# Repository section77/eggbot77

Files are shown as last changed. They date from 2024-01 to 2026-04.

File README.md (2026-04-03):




# eggbot77

Section77-Variante des EggBots mit ESP32 S2 mini

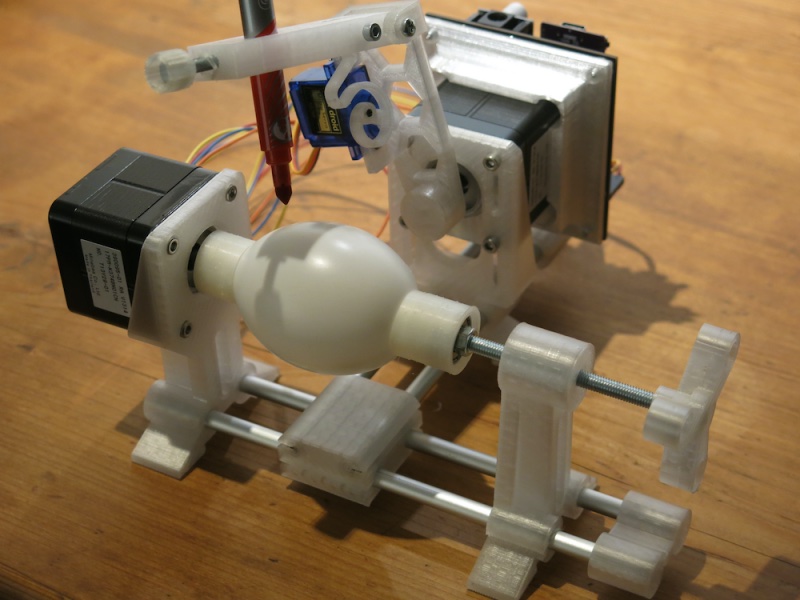
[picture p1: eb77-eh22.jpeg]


Willkommen! :)

Bitte prüfe zuallererst, ob Du alle Komponenten hast, die Du zum Bau Deines EggBot77 brauchst!
* [Materialliste Mechanik](./mechanics/BOM.md)
* [Materialliste Elektronik](./electronics/BOM.md)

Alles da? Super! Dann kann's ja losgehen:
* [Aufbauanleitung Mechanik](./mechanics/assembly/README.md)
* [Aufbauanleitung Elektronik](./electronics/assembly/README.md)
* [Installationsanleitung Firmware](./firmware/README.md)
* [Installationsanleitung Inkscape Plugin](./inkscape_1.x_extension/README.md)

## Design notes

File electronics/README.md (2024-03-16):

Section77 Variante des EggBots mit S2 mini ESP32

Gedanken/Designentscheidungen

## LM2596 Board 1,29€/Stk

für Eingangsspannung -> 5V

Gibt es in zig Varianten, ich habe 20x https://www.amazon.de/Stromversorgung-Spannungsregler-Abwärtswandler-Hocheffizienter-Einstellbares/dp/B07F38DJLS bestellt
Beim Artikel steht Innovateking-EU, ‎Zhovee ‎KKK20 aber keine Aufschrift auf dem Board.

Achtung: Ausgangsspannung am Trimmer einstellen, bevor die anderen Module wie ESP, Schrittmotortreiber, Servo usw. gesteckt werden.
Laut einigen Berichten, muss man mindestens 5 Umdrehungen machen, bevor sich die Ausgangsspannung ändert.

## A4988 carrier board

Ich weiß nicht, was das "original" ist, vermutlich https://www.pololu.com/product/1182
aber es gibt da mittlerweile dutzend Nachbauen, von denen vermutlich viele pinkompatibel sind.
Wir bestellen vermutlich bei https://www.roboter-bausatz.de/p/a4988-schrittmotorentreiber

Microstepping über Lötbrücken einstellbar.

## Netzteile

* https://www.pollin.de/p/polsat-gp1220-a-schaltnetzteil-12-v-2-a-gebraucht-352884 (12V, 2A, Hohlstecker 5,5/2,3 mm, Pluspol innen) - 1,99
* https://www.pollin.de/p/schaltnetzteil-telekom-da-24r12-aaaa-12v-2a-schwarz-352354 (12V, 2A, Hohlstecker 5,5/2,5 mm, Pluspol innen) - 2,50
* https://www.pollin.de/p/stecker-schaltnetzteil-hw-120250eaw-12-v-2-5-a-353145 (12V, 2,5A, Hohlstecker 5,5/2,3 mm, Pluspol innen) - 2,50
* https://www.pollin.de/p/stecker-schaltnetzteil-umec-up0301b-12pe-12v-2-5a-352707 (12V, 2,5A, Hohlstecker 5,5/2,5 mm, Pluspol innen) - 2,95
* https://www.pollin.de/p/stecker-schaltnetzteil-umec-uh0301p-12pe-12v-2-5a-352708 (12V, 2,5A, Hohlstecker 5,5/2,5 mm, Pluspol innen) - 2,95

Hohlbuchsen: Pollin 94-451810 und 94-452316

## S2 mini von Wemos

https://www.wemos.cc/en/latest/s2/s2_mini.html

Für das Board gibt es wohl keine Zeichnung mit Dimensions, siehe auch hier,
wo einer viele Messungen gemacht hat und auch ein Kikad Symbol angefangen hat:
https://gitlab.com/kicad/libraries/kicad-footprints/-/merge_requests/2904

S3 mini hat angeblich gleiches Layout (aber anderes pinning): https://www.wemos.cc/en/latest/_static/files/dim_s3_mini_v1.0.0.pdf

## Stift Servo

um den Stift anzuheben bzw. abzusenken.
Vermutlich https://www.roboter-bausatz.de/p/sg90-9g-micro-servomotor

## Schrittmotoren

Pollin Stepper 94-310690

## Levelshifter

* https://learn.sparkfun.com/tutorials/bi-directional-logic-level-converter-hookup-guide/all
* https://www.digikey.de/de/blog/logic-level-shifting-basics

## Ähnliches Projekt

https://content.instructables.com/FQ1/O4B9/KTWY3YCQ/FQ1O4B9KTWY3YCQ.jpg

Folgende Änderungen:
* SD-Reader entfällt
* Dev-Board durch S2 mini ersetzen
* den 7805 durch step-down ersetzen
* alles sollte THT sein, damit's einfacher zu löten ist

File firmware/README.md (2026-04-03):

## Arduino IDE projects in this directory

* hardware_test: simple programm to check the eggbot77 hardware (both stepper and pen servo) without PC.
  **Attention:** The stepper motors make several fast revolutions. The program should therefore only be executed as long as the servo and stepper motors have not yet been installed.
* EggBott77: firmware which interprets the EBB command set send from the inkscape extension

## Arduino IDE settings common for all projects here

* USB CDC On Boot: "Enabled"
* Controller: LOLIN S2 Mini

## Versions that we have tested successfully with

* Arduino IDE: 2.3.8 (latest as of 2026-03-30)
* esp32: 3.3.7 (latest as of 2026-03-30)

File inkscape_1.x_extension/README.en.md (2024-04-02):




# Inkscape 1.x Extension for EggBot77

## Installation on Linux and OSX
Put the content of the directories `extensions` and `templates` inside the respective folders inside your user extensions folder (the ones listed at `Edit` > `Preferences` under `System: User extensions` and `System: User templates`, by default `~/.config/inkscape/extensions` and `~/.config/inkscape/templates`).

```bash
mkdir -p ~/.config/inkscape/extensions/
mkdir -p ~/.config/inkscape/templates/
cp -r extensions/* ~/.config/inkscape/extensions/
cp -r templates/* ~/.config/inkscape/templates/
```

### Dependencies

- Inkscape >= 1.0 (obviously). We have tested with newer versions up to Inkscape 1.3
- python3
- python3-serial

Note: in case you want to install a newer version of Inkscape, make sure you use the PPA option.

On Debian or Debian-based distributions (Ubuntu, Mint) use apt, for example
```bash
sudo apt install inkscape python3 python3-serial
```
### Permissions

On most GNU/Linux distributions you have to be member of a certain group to use serial ports.

On Debian this is the `dialout` group to which you can add yourself with
```
sudo addgroup $USER dialout
```

On Archlinux it is the `uucp` group to which you can add yourself with
```
sudo usermod -aG uucp $USER
```

Note: You need to logout/logon or reboot to activate the change.

### Troubleshooting

You aren't able to connect to your EggDuino? Try this:

Disconnect your ESP32 board from your PC and execute
```
sudo dmesg -ew
```
and plug your board in again. You should see something like
```
[  +2,039765] usb 3-1: new full-speed USB device number 4 using xhci_hcd
[  +0,183255] usb 3-1: New USB device found, idVendor=303a, idProduct=8141, bcdDevice= 1.00
[  +0,000009] usb 3-1: New USB device strings: Mfr=1, Product=2, SerialNumber=3
[  +0,000003] usb 3-1: Product: DENEYAP MINI
[  +0,000002] usb 3-1: Manufacturer: Turkish Technnology Team Foundation (T3)
[  +0,000001] usb 3-1: SerialNumber: 80:65:99:4b:06:ea
[  +0,037042] cdc_acm 3-1:1.0: ttyACM0: USB ACM device
```

The important pieces you can extract from the above: Your device is now available as `/dev/ttyACM0`. You can now check the permissions which are needed to access this device:

```
$ ls -la /dev/ttyACM0
crw-rw---- 1 root dialout 166, 0  8. Feb 12:41 /dev/ttyACM0
```

So you need to be `root` or are member of the group `dialout`. Are we?
```
$ groups
dialout cdrom floppy sudo audio dip video plugdev netdev lpadmin scanner bluetooth libvirt sbuild libvirt-qemu
```

Be sure the output of `groups` includes the group `dialout` as it does above.

Then start inkscape, select Extensions - EggBot - EggBot Control. On the `Manual` tab you can check the individual commands like pen up/down.

## Installation on Windows
You have to copy the templates and extensions folders to the `share/inkscape` folder which is typically located at `C:\Program Files\Inkscape\share/inkscape`

## Inkscape AppImage

The original Inkscape AppImages are missing the python-serial module and thus won't work out of the box.

You'll find an AppImage where we added the modules and extensions here: https://docs.section77.de/Inkscape-091e20e-EggBot77-x86_64.AppImage

The above linked image was created on Debian GNU/Linux 12 (bookworm) with

```bash
# get Inkscape AppImage
wget -nc https://inkscape.org/de/gallery/item/44616/Inkscape-091e20e-x86_64.AppImage
chmod +x Inkscape-091e20e-x86_64.AppImage

# extract it
./Inkscape-091e20e-x86_64.AppImage --appimage-extract

# add pyserial
wget -nc https://files.pythonhosted.org/packages/1e/7d/ae3f0a63f41e4d2f6cb66a5b57197850f919f59e558159a4dd3a818f5082/pyserial-3.5.tar.gz
tar xzf pyserial-3.5.tar.gz
cp -r pyserial-3.5/serial squashfs-root/usr/lib/python3/dist-packages/

# add EggBot77 extensions and template
cp ./extensions/* squashfs-root/usr/share/inkscape/extensions/
cp ./templates/* squashfs-root/usr/share/inkscape/templates/

# repack the AppImage
wget -nc https://github.com/AppImage/AppImageKit/releases/download/continuous/appimagetool-x86_64.AppImage
chmod +x appimagetool-x86_64.AppImage
./appimagetool-x86_64.AppImage squashfs-root/

# rename it
mv Inkscape-x86_64.AppImage Inkscape-091e20e-EggBot77-x86_64.AppImage
```

## Credits

This directory started as
```bash
git clone -b inkscape1.0compat https://github.com/gesina/eggbot_extension.git
```

and went further from there. The reason for this was the wish to have one complete repo with PCB, 3D printing parts, ESP32 firmware and inkscape plugin without the need to fiddle around with subrepos which may break compatibility over time.

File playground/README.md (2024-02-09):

various scripts to describe an egg mathematically, for example, or to play a midi file on the stepper motors.

Requires GNU Octave

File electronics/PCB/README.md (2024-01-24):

Design rule file jlcpcb-2layers.dru from https://github.com/oxullo/jlcpcb-eagle

CAM File for Eagle 7.7 from
https://raw.githubusercontent.com/JLCPCBofficial/jlcpcb-eagle/master/cam/jlcpcb_2_layer_v72.cam

linked from https://jlcpcb.com/help/article/9-How-to-Generate-Gerber-and-Drill-Files-in-Autodesk-Eagle

Notes when ordering at jlcpcb. From above help page:

  "Just to be safe, you can write a special instruction in the remark area in our
  ordering system when you place the order, write like:
  "Please note: there are 3 plated slotted holes in this design".
  Our CAM engineer will sort them out from the "context"
  (like the annular ring and solder mask opening) when processing the files."

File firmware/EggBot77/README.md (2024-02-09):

EggBot77
====

ESP32 S2 mini firmware

Cloned from https://github.com/Andy1978/EggDuino, adapted to the new
EggBot77 board based on ESP32 S2 Mini.

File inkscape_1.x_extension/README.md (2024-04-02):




# Inkscape 1.x Erweiterung für EggBot77

## Installation unter Linux und OSX
Kopiere den Inhalt der Verzeichnisse `extensions` und `templates` in die entsprechenden Ordner unterhalb des Verzeichnisses mit Deinen Erweiterungen (die unter `Bearbeiten` > `Einstellungen` unter `System: Benutzererweiterungen` und `System: Benutzervorlagen`, standardmäßig `~/.config/inkscape/extensions` und `~/.config/inkscape/templates`).

```bash
mkdir -p ~/.config/inkscape/extensions/
mkdir -p ~/.config/inkscape/templates/
cp -r extensions/* ~/.config/inkscape/extensions/
cp -r templates/* ~/.config/inkscape/templates/
```

### Abhängigkeiten

- Inkscape >= 1.0 (offensichtlich). Wir haben auch mit neueren Version bis Inkscape 1.3 getestet
- python3
- python3-serial

Anmerkung: falls Du eine neuere Version von Inkscape installieren möchtest, verwende die PPA-Variante

Verwende auf Debian oder Debian-basierten Distributionen (Ubuntu, Mint) apt, zum Beispiel
```bash
sudo apt install inkscape python3 python3-serial
```

### Zugriffsrechte

Bei den meisten GNU/Linux-Distributionen muss man Mitglied einer bestimmten Gruppe sein, um die serielle Schnittstellen nutzen zu können.

Unter Debian ist dies die Gruppe `dialout`, zu der Du Dich hinzufügen kannst mit
```
sudo addgroup $USER dialout
```

Unter Archlinux ist es die Gruppe `uucp`, zu der Du Dich selbst hinzufügen kannst mit
```
sudo usermod -aG uucp $USER
```

Anmerkung: melde Dich ab und wieder an, um die Änderung zu aktivieren.

### Fehlersuche

#### Du kannst keine Verbindung zu Ihrem EggDuino herstellen? 

Versuch' das:

Trenne Dein ESP32-Board von Deinem PC, führe aus
```
sudo dmesg -ew
```
und schließe Dein Board wieder an. Du solltest etwas sehen wie
```
[  +2,039765] usb 3-1: new full-speed USB device number 4 using xhci_hcd
[  +0,183255] usb 3-1: New USB device found, idVendor=303a, idProduct=8141, bcdDevice= 1.00
[  +0,000009] usb 3-1: New USB device strings: Mfr=1, Product=2, SerialNumber=3
[  +0,000003] usb 3-1: Product: DENEYAP MINI
[  +0,000002] usb 3-1: Manufacturer: Turkish Technnology Team Foundation (T3)
[  +0,000001] usb 3-1: SerialNumber: 80:65:99:4b:06:ea
[  +0,037042] cdc_acm 3-1:1.0: ttyACM0: USB ACM device
```

Die wichtigsten Informationen kannst Du aus den obigen Angaben entnehmen: Dein Gerät ist jetzt als `/dev/ttyACM0` verfügbar. Du kannst nun die Rechte überprüfen, die für den Zugriff auf dieses Gerät erforderlich sind:

```
$ ls -la /dev/ttyACM0
crw-rw---- 1 root dialout 166, 0 8. Feb 12:41 /dev/ttyACM0
```

Du musst also `root` sein oder Mitglied der Gruppe `dialout`. Bist Du das?
```
$ groups
dialout cdrom floppy sudo audio dip video plugdev netdev lpadmin scanner bluetooth libvirt sbuild libvirt-qemu
```

Vergewissere Dich, dass die Ausgabe von `groups` die Gruppe `dialout` enthält, wie es oben der Fall ist.

Starte dann Inkscape, wähle `Erweiterungen - EggBot - EggBot Control`. Auf der Registerkarte `Manual` kannst Du die einzelnen Befehle wie `Pen up`/`Pen down` testen.

## Installation unter Windows
Die Ordner `templates` und `extensions` müssen in den Ordner `share/inkscape` kopiert werden, der normalerweise unter `C:\Programme\Inkscape\share\inkscape` zu finden ist.

## Inkscape AppImage

Den originalen Inkscape AppImages fehlt das Modul `python-serial` und sie funktionieren daher nicht ohne weiteres.

Ein AppImage, bei dem wir die Module und Erweiterungen hinzugefügt haben, findest Du hier: https://docs.section77.de/Inkscape-091e20e-EggBot77-x86_64.AppImage

Das oben verlinkte Image wurde auf Debian GNU/Linux 12 (bookworm) mit

```bash
# Inkscape AppImage holen
wget -nc https://inkscape.org/de/gallery/item/44616/Inkscape-091e20e-x86_64.AppImage
chmod +x Inkscape-091e20e-x86_64.AppImage

# entpacken
./Inkscape-091e20e-x86_64.AppImage --appimage-extract

# pyserial hinzufügen
wget -nc https://files.pythonhosted.org/packages/1e/7d/ae3f0a63f41e4d2f6cb66a5b57197850f919f59e558159a4dd3a818f5082/pyserial-3.5.tar.gz
tar xzf pyserial-3.5.tar.gz
cp -r pyserial-3.5/serial squashfs-root/usr/lib/python3/dist-packages/

# EggBot77-Erweiterungen und -Vorlage hinzufügen
cp ./extensions/* squashfs-root/usr/share/inkscape/extensions/
cp ./templates/* squashfs-root/usr/share/inkscape/templates/

# AppImage neu packen
wget -nc https://github.com/AppImage/AppImageKit/releases/download/continuous/appimagetool-x86_64.AppImage
chmod +x appimagetool-x86_64.AppImage
./appimagetool-x86_64.AppImage squashfs-root/

# umbenennen
mv Inkscape-x86_64.AppImage Inkscape-091e20e-EggBot77-x86_64.AppImage
```

## Credits

Dieses Verzeichnis begann als
```bash
git clone -b inkscape1.0compat https://github.com/gesina/eggbot_extension.git
```

und wuchs von dort aus weiter. Der Grund dafür war der Wunsch, eine komplette Repo mit PCB, 3D-Druckteilen, ESP32-Firmware und Inkscape-Plugin zu haben, ohne ohne mit Unterrepos herumspielen zu müssen, die mit der Zeit die Kompatibilität beeinträchtigen könnten.

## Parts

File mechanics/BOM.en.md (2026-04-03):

## BOM mechanics

### Motors
* Stepper NEMA17 (1x with a square axis 3x3 mm and 1x with a gear)
* Micro Servo SG90 (1x)

### 3d printed parts
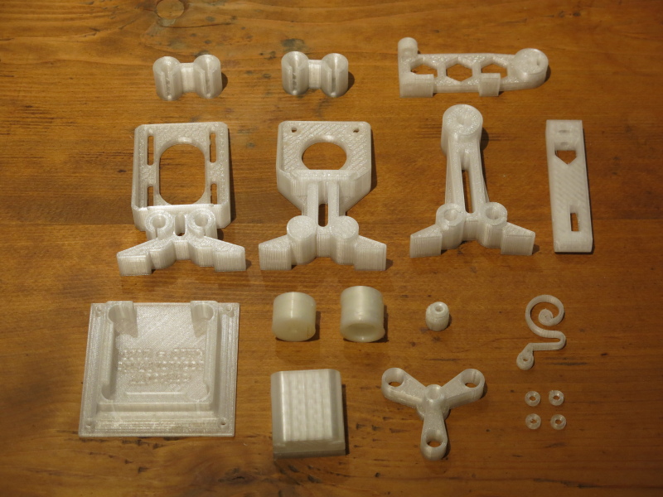
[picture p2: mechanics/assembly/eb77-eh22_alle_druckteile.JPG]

* [Tail stock holder](./print_files/tailstock_V2.stl)
* [Faucet](./print_files/Faucet.stl)
* [Egg holder bearing side](./print_files/tpu-eierhalter-lagerseite.stl)
* [Nut knob](./print_files/nut_knob_v1_5_1_M4.stl)
* [Tool mount](./print_files/toolmount.stl)
* [Spring](./print_files/spring-3mm.stl)
* [Pen arm](./print_files/penarm-strongerV2.stl)
* [PCB holder](./print_files/nema-eggbot77-mount.stl)
* [Spacer](./print_files/spacer.stl)
* [Intersecting box](./print_files/Box_IntersectionNew.stl)
* [stepperholder for the pen](./print_files/stepperholderV4.stl)
* [rotational stepper holder](./print_files/Rotational_Stepper_HolderV2.stl)
* [Eierhalter Motorseite](./print_files/tpu-eierhalter-stiftseite.stl)

#### Amount of filament used  (20% infill): 
  * PLA: some 110g
  * TPU: some 11g

### Screws and bolts
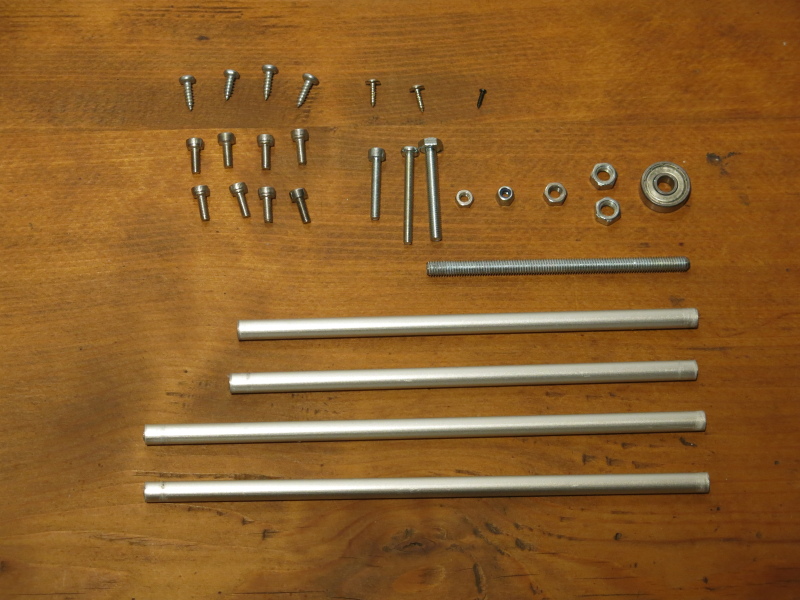
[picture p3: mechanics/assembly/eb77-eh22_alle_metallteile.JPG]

* Bolt M4x30 (1x; holding the pen)
* Nut M4 (1x; holding the pen)
* Bolt M3x30 lens head (1x; for the hinge)
* Bolt M3x20 counter sunk head (1x; for the intersecting box)
* Bolt M3x20 cylindrical head (1x; holding the spring)
* Bolt M3x8 cylindrical head (8x; holding the steppers)
* Nut M3 (3x; 1x for the intersecting box and 2x for the pen arm)
* Nut M5 (2x; holding the bearing)
* Screw 3x12mm (4x; holding the PCB)
* Screw 2mm (1x; attaching the spring to the servo horn; not in the picture!)
* Threaded rod M5 ca. 10cm (1x; holding the egg)

### Miscellaneous components
* Bearing 625ZZ
* Aluminum rod 6mmm, ca. 12,5cm (2x)
* Aluminum rod 6mmm, ca. 16,5cm (2x)

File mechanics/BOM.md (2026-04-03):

## Materialliste Mechanik

### Motoren
* Schrittmotor NEMA17 (1x mit quadratischer Achse 3x3 mm und 1x mit Zahnrad)
* Micro-Servo SG90 (1x)

### Ausdrucke

* [Reitstockhalter](./print_files/tailstock_V2.stl)
* [Wasserhahn](./print_files/Faucet.stl)
* [Eierhalter Lagerseite](./print_files/tpu-eierhalter-lagerseite.stl)
* [Griff](./print_files/nut_knob_v1_5_1_M4.stl)
* [Werkzeughalter](./print_files/toolmount.stl)
* [Feder](./print_files/spring-3mm.stl)
* [Stiftarm](./print_files/penarm-strongerV2.stl)
* [Platinenhalter](./print_files/nema-eggbot77-mount.stl)
* [Abstandhalter](./print_files/spacer.stl)
* [Zentrum](./print_files/Box_IntersectionNew.stl)
* [Stepperhalter für den Stift](./print_files/stepperholderV4.stl)
* [Rotationsstepperhalter](./print_files/Rotational_Stepper_HolderV2.stl)
* [Eierhalter Motorseite](./print_files/tpu-eierhalter-stiftseite.stl)

#### Benötigte Filamentmenge (20% Infill): 
  * PLA: ca. 110g
  * TPU: ca. 11g

### Schrauben

* Schraube M4x30 (1x; zur Fixierung des Stiftes)
* Mutter M4 (1x; zur Fixierung des Stiftes)
* Schraube M3x30 Linsenkopf (1x; für das Armgelenk)
* Schraube M3x20 Zylinderkopf (1x; zur Befestigung der Feder)
* Schraube M3x8 Zylinderkopf (8x; zur Befestigung der Schrittmotoren)
* Stopmutter M3 (1x; für das Lager des Stiftarms)
* Mutter M3 (1x; zur Fixierung der Feder am den Stiftarm)
* Mutter M5 (2x; zur Befestigung des Lagers)
* Blechschraube 3x12mm (4x; zur Befestigung der Platine)
* Blechschraube 2mm (1x; zur Befestigung der Feder am Servohorn; nicht im Bild!)
* Blechschraube 2mm (2x; zur Befestigung des Servos am Stiftarm; nicht im Bild!)
* Gewindestange M5 ca. 10cm (1x; zur Fixierung des Eis)

### Sonstige Komponenten
* Lager 625ZZ
* Alustange 6mmm, ca. 12 cm (2x)
* Alustange 6mmm, ca. 15 cm (2x)

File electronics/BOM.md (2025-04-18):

### optional für 5V PWM Pegel am Servo

* 1x BSS 138 SMD (MOSFET, N-CH, 50V, 0,22A, 0,36W, SOT-23) 0,07€
* 2x WAL WR12X4701FTL (SMD-Widerstand, 1206, 4,7 kOhm, 250 mW, 1%) 0,02€

| Kategorie  | Bauteil | Anzahl | Shop (Bsp.) | Quelle (Bsp.) |
| --- | --- | --- | --- | --- |
| Elektronik | Platine | 1 | - | - |
| Elektronik | Schottkydiode 1N 5822 (40 V, 3 A, DO-201AD) | 1 | Reichelt | [Quelle](https://www.reichelt.de/schottkydiode-40-v-3-a-do-201ad-1n-5822-p41852.html) |
| Elektronik | Elko 100 µF (RAD FR 100/35, d = 8, L = 11.5 950mA @ 100kHz, 56 mOhm, 3,5mm Beinabstand,  radial) | 2 | Reichelt | [Quelle](https://www.reichelt.de/elko-radial-100-f-35v-105-c-low-esr-rad-fr-100-35-p140121.html) |
| Elektronik | Stiftleiste 1x8-polig (SL 1X8G, gerade, RM 2,54) | 3 |
| Elektronik | Netzteil 12V (Hohlstecker 5,5/2,5 mm, Pluspol innen) | 1 | Pollin | [Quelle](https://www.pollin.de/p/stecker-schaltnetzteil-umec-up0301b-12pe-12v-2-5a-b-ware-352707) |
| Elektronik | Hohlbuchse (Printmontage, 5,5/2,1 mm, 94-452316) | 1 | Pollin | [Quelle](https://www.pollin.de/p/hohlbuchse-printmontage-5-5-2-1-mm-452316) |
| Elektronik | Buchsenleiste 2x8-polig (451354 CONNFLY ELECTRONIC, vergoldet)  | 2 | Conrad
| Elektronik | Buchsenleiste 1x20-polig (451498 CONNFLY ELECTRONIC, vergoldet) | 2 |
| Elektronik | Buchsenleiste 1x8-polig | 1 |
| Elektronik | Spannungswandlermodul (LM2596 DC-DC) | 1 | Roboter-Bausatz | [Quelle](https://www.roboter-bausatz.de/p/spannungswandler-lm2596s-dc-dc-step-down-modul-2a) |
| Elektronik | Microcontroller (ESP32 S2 mini) | 1 |
| Elektronik | JST-Stiftleiste PH6P ST (gerade, 1x6-polig - PH) | 2 | Reichelt | [Quelle](https://www.reichelt.de/jst-stiftleiste-gerade-1x6-polig-ph-jst-ph6p-st-p185053.html?&trstct=pos_0&nbc=1) |
| Elektronik | Schrittmotortreiber Polulu A4988 | 2 | Roboter-Bausatz | [Quelle]( https://www.roboter-bausatz.de/p/a4988-schrittmotorentreiber) |
| Elektronik | USB-Zuleitung | 1 | | |

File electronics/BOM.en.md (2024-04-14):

### optional for 5V PWM level for the servo

* 1x BSS 138 SMD (MOSFET, N-CH, 50V, 0,22A, 0,36W, SOT-23) 0,07€
* 2x WAL WR12X4701FTL (SMD resistor, 1206, 4,7 kOhm, 250 mW, 1%) 0,02€

| Category | Component | Number | Shop (example) | Source (example) |
| --- | --- | --- | --- | --- |
| Elektronik | Platine | 1 | - | - |
| Elektronik | Schottkydiode 1N 5822 (40 V, 3 A, DO-201AD) | 1 | Reichelt  | [Quelle](https://www.reichelt.de/schottkydiode-40-v-3-a-do-201ad-1n-5822-p41852.html) |
| Elektronik | Elko 100 µF (RAD FR 100/35, d = 8, L = 11.5 950mA @ 100kHz, 56 mOhm, 3,5mm Beinabstand,  radial) | 2 | Reichelt | [source](https://www.reichelt.de/elko-radial-100-f-35v-105-c-low-esr-rad-fr-100-35-p140121.html) |
| Elektronik | Stiftleiste 1x36-polig (SL 1X36G, gerade, RM 2,54) | 1 |
| Elektronik | Netzteil 12V (Hohlstecker 5,5/2,5 mm, Pluspol innen) | 1 | Pollin | [Source](https://www.pollin.de/p/stecker-schaltnetzteil-umec-up0301b-12pe-12v-2-5a-b-ware-352707) |
| Elektronik | Hohlbuchse (Printmontage, 5,5/2,1 mm, 94-452316) | 1 | Pollin | [Source](https://www.pollin.de/p/hohlbuchse-printmontage-5-5-2-1-mm-452316) |
| Elektronik | Buchsenleiste 2x8-polig (451354 CONNFLY ELECTRONIC, vergoldet)  | 2 | Conrad
| Elektronik | Buchsenleiste 1x20-polig (451498 CONNFLY ELECTRONIC, vergoldet) | 2 |
| Elektronik | Schrittmotortreiber | 2 |
| Elektronik | Spannungswandlermodul (LM2596 DC-DC) | 1 | Amazon | [Source](https://www.amazon.de/Stromversorgung-Spannungsregler-Abwärtswandler-Hocheffizienter-Einstellbares/dp/B07F38DJLS) |
| Elektronik | Microcontroller (ESP32 S2 mini) | 1 |
| Elektronik | JST-Stiftleiste PH6P ST (gerade, 1x6-polig - PH) | 2 | Reichelt | [Source](https://www.reichelt.de/jst-stiftleiste-gerade-1x6-polig-ph-jst-ph6p-st-p185053.html?&trstct=pos_0&nbc=1) |
| Elektronik | Stepper driver Polulu A4988 | 2 | Roboter-Bausatz | [Source]( https://www.roboter-bausatz.de/p/a4988-schrittmotorentreiber) |

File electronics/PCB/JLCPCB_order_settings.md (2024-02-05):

## JLCPCB order from 25.01.2024

Default settings after uploading eggbot77_gerber.zip to https://jlcpcb.com/ are marked with (*)

* Base Material: FR-4 (*)
* Layers: 2 (*)
* Dimensions 70x70mm (*)
* PCB Qty: 15
* Product Type: Industrial/Consumer electronics  (*)
* Different Design: 1  (*)
* Delivery Format: Single PCB  (*)
* PCB Thickness: 1.6  (*)
* PCB Color: Black
* Silkscreen: White (*)
* Surface Finish: LeadFree HASL
* Outer Copper Weight: 1oz (*)
* Via Covering: Untented
* Board Outline Tolerance: +/- 0.2mm(Regular) (*)
* Confirm Production file: No (*)
* Remove Order Number: No (*)
* Fyling Probe Test: Fully Test (*)
* Gold Fingers: No (*)
* Castellated Holes: No (*)
* Edge Plating: No (*)
* PCB Remark: "Please note: there are 3 plated slotted holes in this design"

* Shipping Method: DDP EuroPacket (*)

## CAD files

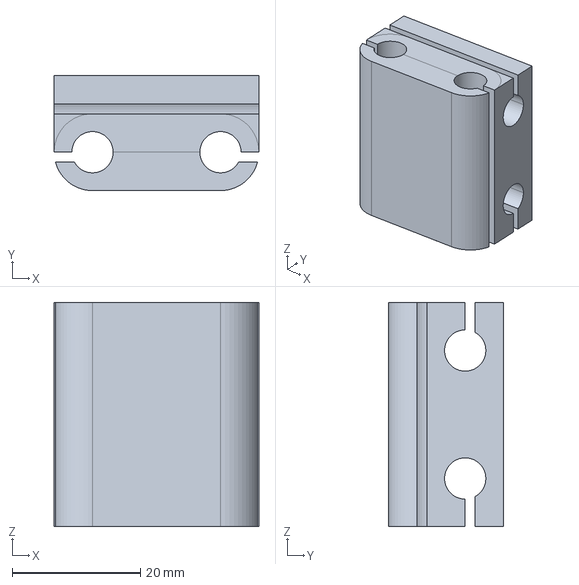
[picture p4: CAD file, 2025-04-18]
mechanics/print_files/source/Box_IntersectionNew.FCStd
32.0 x 18.0 x 35.0 mm

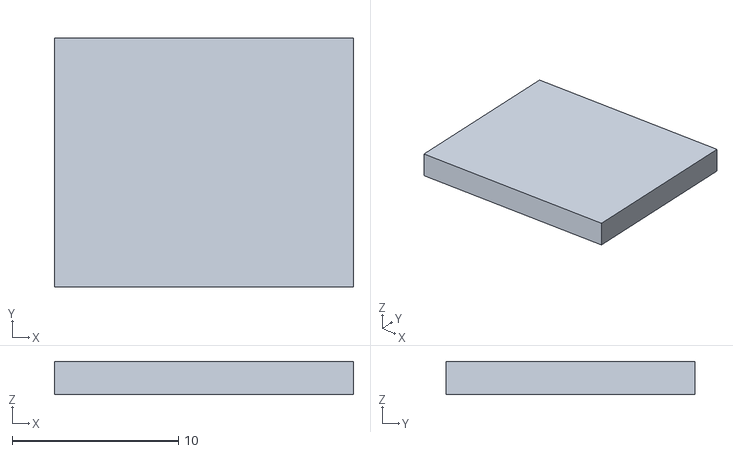
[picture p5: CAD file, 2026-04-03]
mechanics/print_files/tpu-pad-18x15.stl
18.0 x 15.0 x 2.00

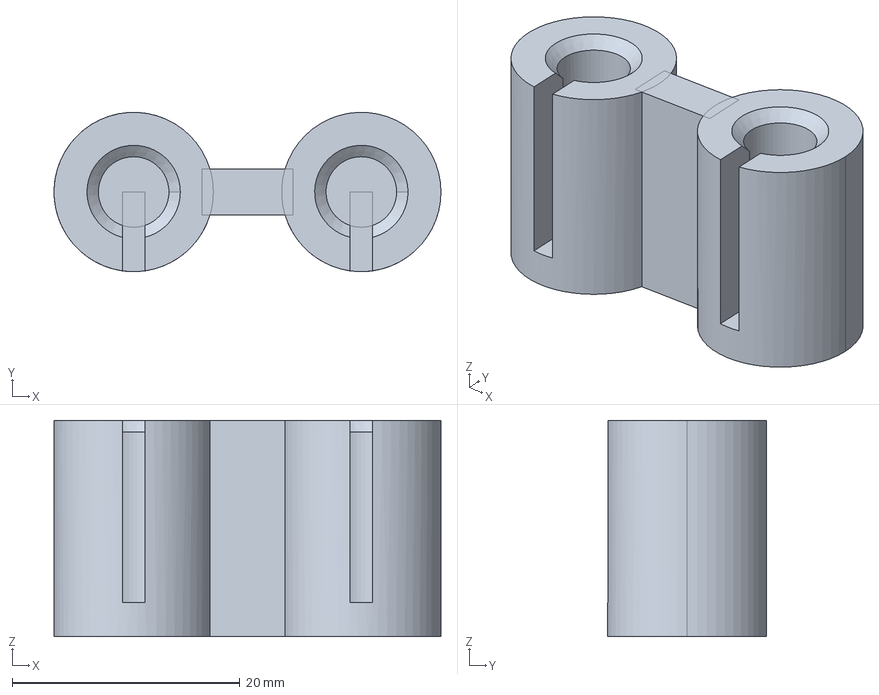
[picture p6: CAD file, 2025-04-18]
mechanics/print_files/source/Protection_Foot.FCStd
34.0 x 14.0 x 19.0 mm

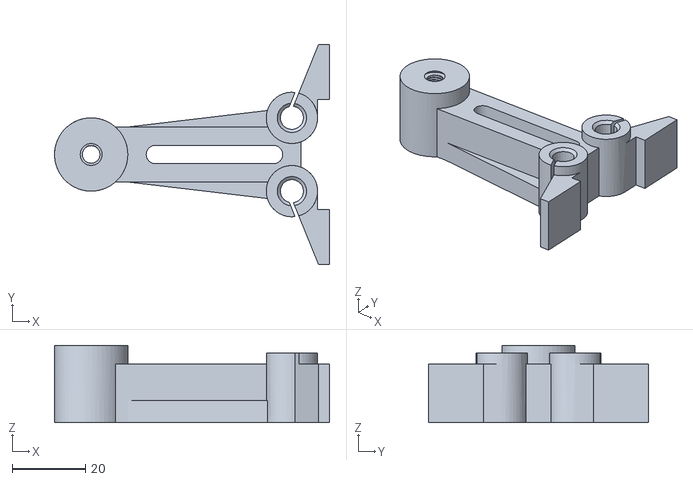
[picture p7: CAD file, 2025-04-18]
mechanics/print_files/tailstock_V2.stl
75.0 x 60.0 x 21.0

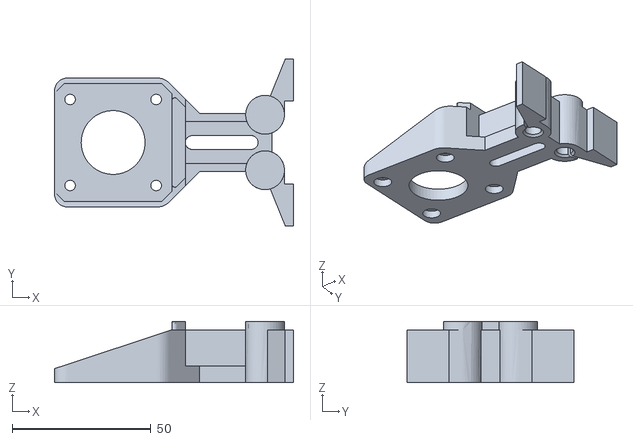
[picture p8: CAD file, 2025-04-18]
mechanics/print_files/Rotational_Stepper_HolderV2.stl
86.1 x 60.0 x 22.0

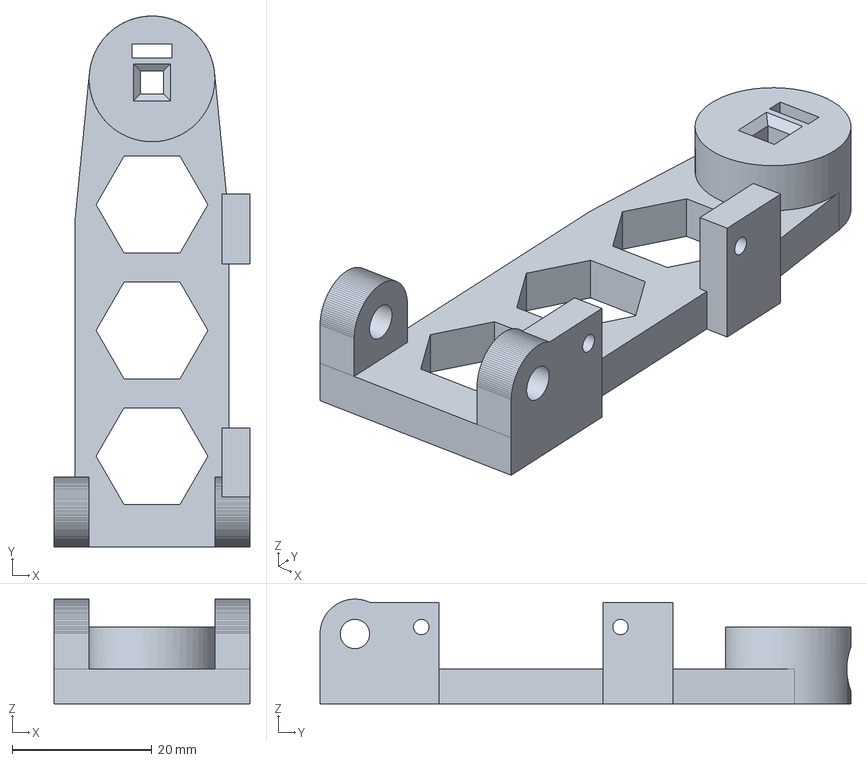
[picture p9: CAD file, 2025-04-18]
mechanics/print_files/source/penarm-strongerV2.FCStd
28.0 x 76.0 x 15.0 mm

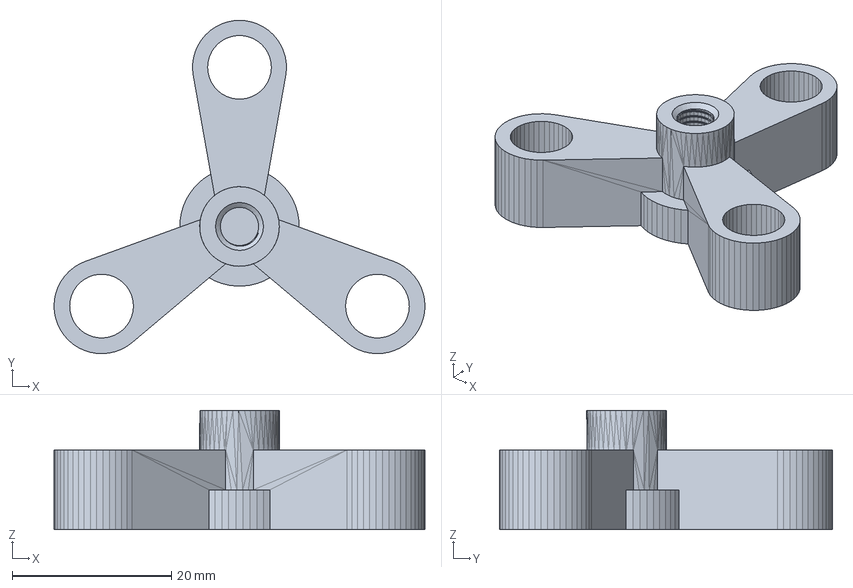
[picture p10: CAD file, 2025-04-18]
mechanics/print_files/source/Faucet.FCStd
46.6 x 41.9 x 15.0 mm

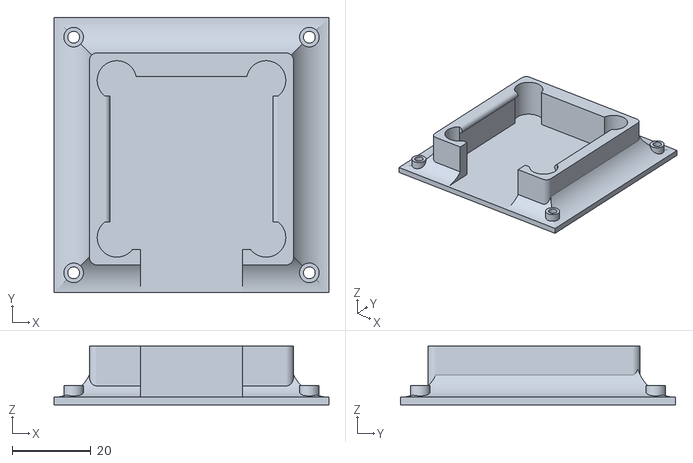
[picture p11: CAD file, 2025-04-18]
mechanics/print_files/nema-eggbot77-mount.stl
70.0 x 70.0 x 15.0

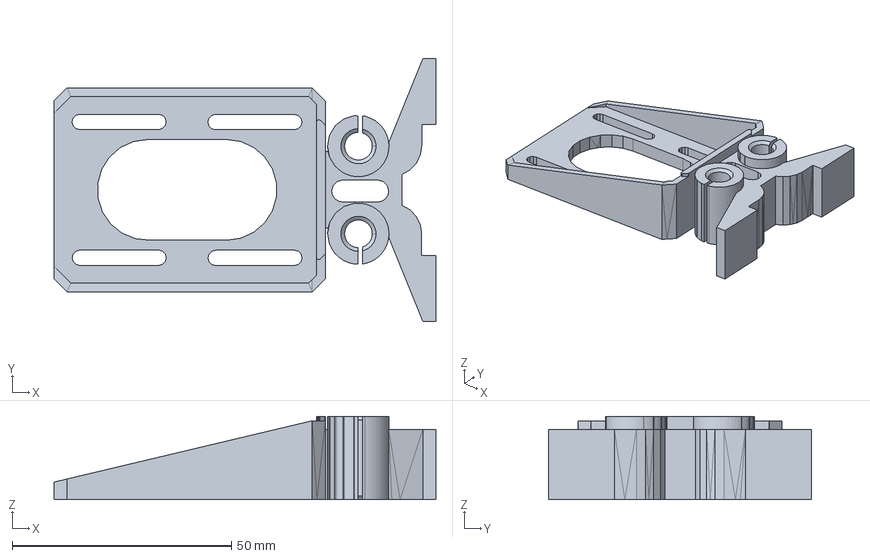
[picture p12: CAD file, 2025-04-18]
mechanics/print_files/source/stepperholderV4.FCStd
87.2 x 60.0 x 19.0 mm

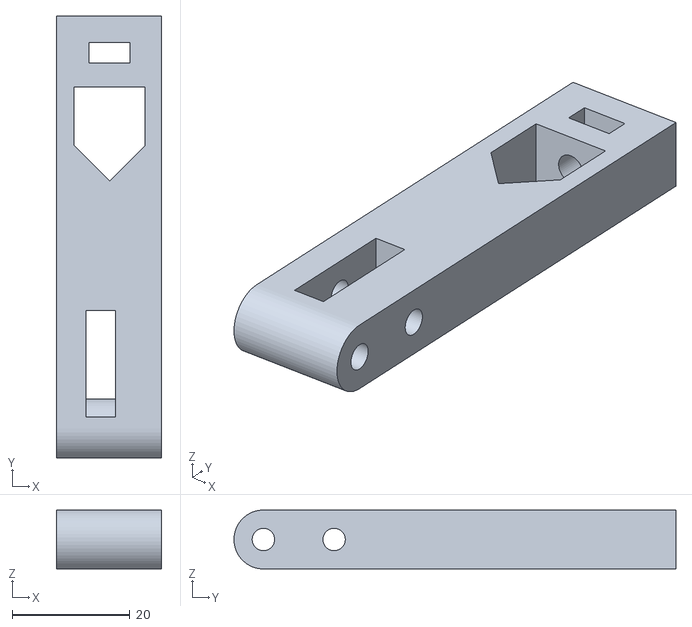
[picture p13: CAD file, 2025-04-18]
mechanics/print_files/toolmount.stl
17.8 x 75.0 x 10.0

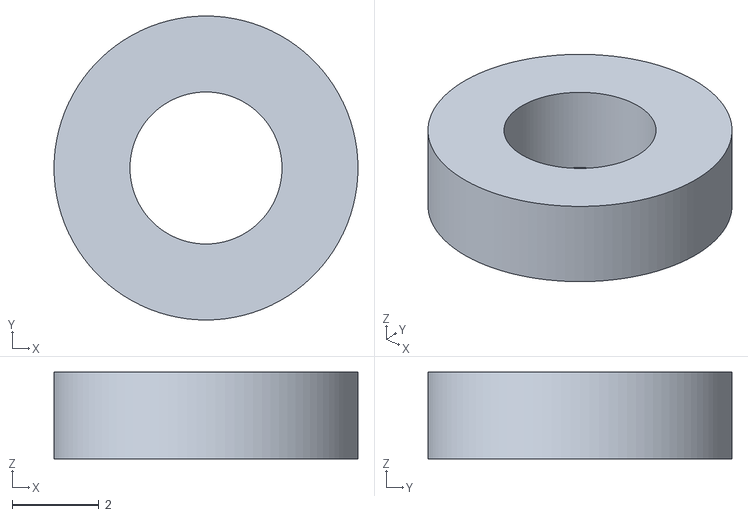
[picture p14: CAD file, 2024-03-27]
mechanics/print_files/spacer.stl
7.00 x 7.00 x 2.00

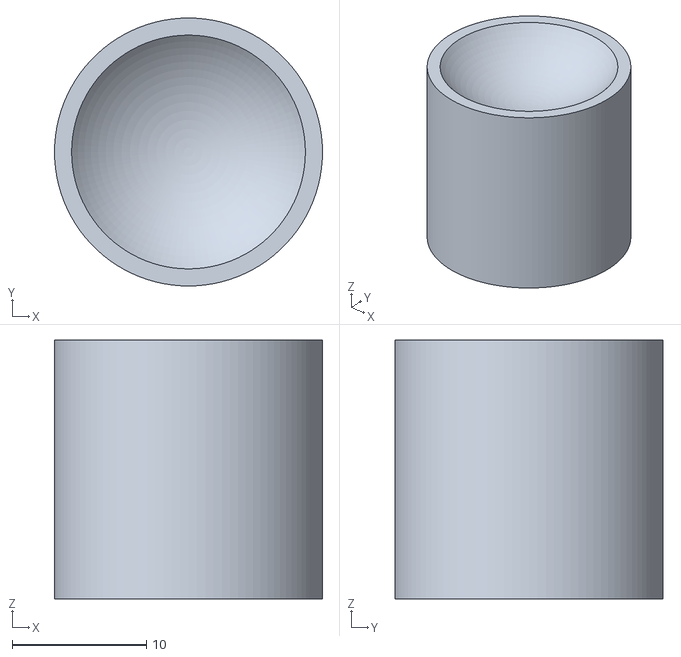
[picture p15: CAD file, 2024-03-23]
mechanics/print_files/tpu-eierhalter-lagerseite.stl
20.0 x 20.0 x 19.3

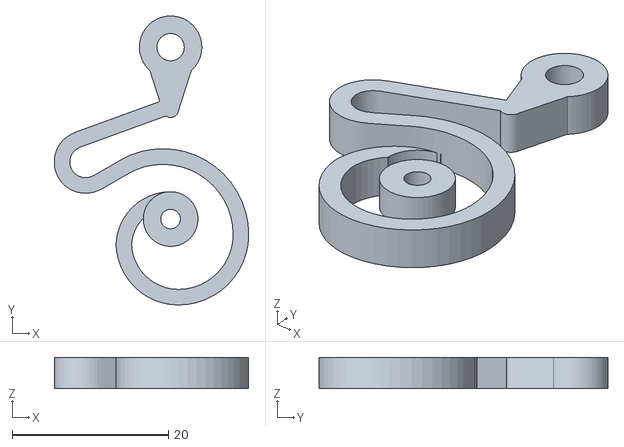
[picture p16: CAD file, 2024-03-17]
mechanics/print_files/spring-3mm.stl
24.9 x 37.0 x 4.00

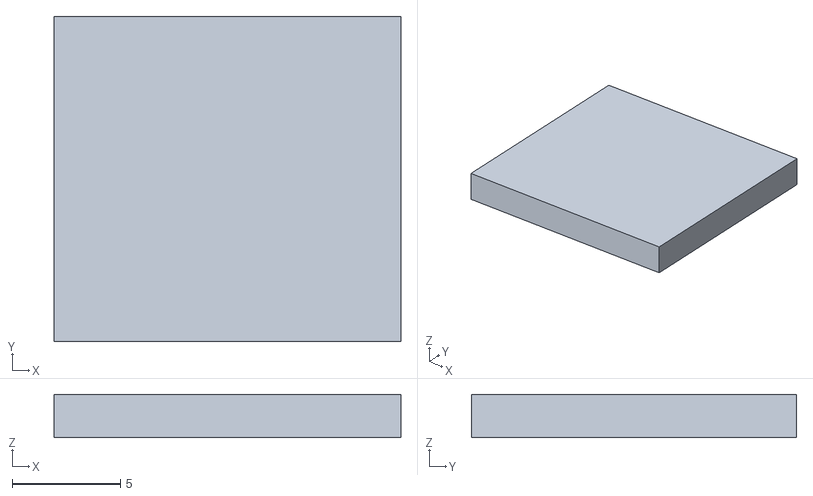
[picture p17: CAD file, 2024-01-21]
mechanics/print_files/tpu-pad-16x15.stl
16.0 x 15.0 x 2.00

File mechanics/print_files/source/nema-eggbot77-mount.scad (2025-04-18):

$fn=100;
drill=[[65,5],[65,65],[5,5],[5,65]];

difference(){
  union(){
    for (i=[0:1:3]){
      bolzen(drill[i],5,2,5);
    }
    translate([0,0,0])cube([70,70,2]);
    translate([35,32,0])mmount(15);
    translate([0,0,2]) difference() {
      union() {
        translate([0,8,0])                    cube([10,62,10]);
        translate([0,70,10]) rotate([90,90,0]) cube([10,70,10]);
        translate([60,8,10]) rotate([0,90,0]) cube([10,62,10]);
        translate([0,8,10]) rotate([90,90,0]) cube([10,70,8]);
      }
    
      translate([0, 70.01,10]) rotate([90,0,0])  cylinder(r=10, h=70.02);
      translate([0, 70.01,10]) rotate([90,0,90]) cylinder(r=10, h=70.02);
      translate([70,70.01,10]) rotate([90,0,0])  cylinder(r=10, h=70.02);
      translate([0,0.01,10]) rotate([90,0,90]) cylinder(r=10, h=70.02);
    }

  }
  for (i=[0:1:3]){
    loecher(drill[i],5,3,15);
  }
  translate([22,-6.9,2.002])cube([26,20.1,30]);
  translate([22,49,8])rotate([0,90,0])difference(){
    cylinder(r=6,h=4);
    translate([0,0,-0.01])cylinder(r=4,h=5);
  }
}

module bolzen(pos,ad,id,ho){
    translate([pos[0],pos[1],0]){
      cylinder(r=ad/2,h=ho);
    }
}

module loecher(pos,ad,id,ho){
    translate([pos[0],pos[1],0]){
      translate([0,0,-0.01])cylinder(r=id/2,h=ho+0.2);
    }
}

module mmount(hm){
  difference(){
    hull(){
			aa=23;
      rd=2;
      translate([-aa-1,-aa,0])cylinder(r=2,h=hm);
      translate([aa+1,-aa,0])cylinder(r=2,h=hm);
      translate([aa+1,aa+4,0])cylinder(r=2,h=hm);
      translate([-aa-1,aa+4,0])cylinder(r=2,h=hm);
    } 
      ai=18;		
      translate([-22,-21,-0.01])cube([44,44,hm+1]);
			translate([-ai-1,-ai,0])cylinder(r=5,h=hm+1);
      translate([ai+1,-ai,0])cylinder(r=5,h=hm+1);
      translate([ai+1,ai+4,0])cylinder(r=5,h=hm+1);
      translate([-ai-1,ai+4,0])cylinder(r=5,h=hm+1);
		}
		translate([22,-14,hm-1.25])rotate([-90,0,0])
      cylinder(r=1.256,h=32);
		translate([-22,-14,hm-1.25])rotate([-90,0,0])
      cylinder(r=1.256,h=32);    
  }

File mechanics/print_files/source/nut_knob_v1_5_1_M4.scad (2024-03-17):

// 'Ultimate Nut Knob Generator' by wstein 
// is licensed under the Attribution - Non-Commercial - Share Alike license. 
// Version 1.5 (c) April 2015
// please refer the complete license here: http://creativecommons.org/licenses/by-nc-sa/3.0/legalcoe
//
// V1.1: some smaller improvements and new parameter "supportless_friendly" and "screw_hole_length"
// V1.2: flip very long knobs (miniature hex handle) and new hex shape
// V1.5: new support of tetragon up to octagon nuts
//       new wing shape
//       error in calulation of nuts fixed (relevant on bigger ones)
// V1.5.1: Global fix for latest Customizer

// preview[view:west, tilt:top diagonal]

//to show in Customizer - you get always all parts!
part = "clamp"; // [hex,simple,cylindrical,clamp,rounded,wing]

//across flats (M3 = 5.42, Allen = 6.35)
nut_width = 6.5;
nut_thickness = 2.6;

//of knob
height=12;

// in percent of knob height
knurled_height=70; //[10:100]

/*[Advanced]*/
echo("nut_diameter",nut_diameter);

// calculated relative to hex nut diameter
diameter_1=100; //[100:300]
function get_diameter_1()=hex_nut_diameter*diameter_1/100;

// in percent of Diameter 1 
diameter_2=140; //[100:200]
function get_diameter_2()=get_diameter_1()*diameter_2/100;

// in percent of nut diameter
screw_hole_diameter = 55; //[0:100]
function get_screw_hole_diameter()=nut_diameter*screw_hole_diameter/100;

// in percent of knob height
screw_hole_length = 100; //[0:100]
function get_screw_hole_length()=height*screw_hole_length/100;

// should be multiple of layer thickness (0.6 should be perfect for 0.1, 0.2, 0.3mm layer thickness). Use 0 for open bottom like the screwdriver handle
bottom_thickness = 1.5;

/*[Knurled]*/
//no effect on wing style
knurled_density=65; //[0:100]

knurled_strong=4;//[1:20]

/*[Expert]*/

//- tetragon=4, pentagon=5, hexagon=6, octagon=8
nut_sides=6;//[4,5,6,8]

// prevented some extreme overhangs
supportless_friendly=1; //[0:false,1:true]

//increase if it fits to tight
backlash=0.1;

cross_section=0; //[0:false,1:true]

/*[Hidden]*/
function get_knurled_n()= (
    part=="hex" ? 6 : (
    part=="wing" ? 2 : (
    round(sqrt(10*get_diameter_2())*get_knurled_density_factor()))));
    
function get_knurled_density_factor()=pow(10,knurled_density/50-1);
echo("get_knurled_density_factor()", get_knurled_density_factor());

nut_diameter = nut_width/cos(360/nut_sides/2);
hex_nut_diameter = nut_width/cos(360/6/2);

knurled_r=sqrt(10*get_diameter_2())/40*knurled_strong;

h1=height-height*knurled_height/100;
hlist=[0,h1/5,h1*2/5,h1*3/5,h1*4/5,h1,height];
rstep=[0,pow(0.2,2),pow(0.4,2),pow(0.6,2),pow(0.8,2),pow(1.0,2),pow(1.0,2)];
rlist=rstep*(get_diameter_2()-get_diameter_1());

if(height-h1-2.1*knurled_r>0||part!="rounded")
rotate(nut_width*5<height?[0,90,0]:(bottom_thickness==0.0?[180,0,0]:[0,0,0]))
union()
{
	difference()
	{
		union()
		{
			create_knurled();
	
			for(n=[0:5])
			translate([0,0,hlist[n]])
			cylinder(r1=(get_diameter_1()+rlist[n])/2,r2=(get_diameter_1()+rlist[n+1])/2,h=hlist[n+1]-hlist[n],$fn=100);
		}
	
		if(get_screw_hole_diameter()>0&&screw_hole_length>0)
		translate([0,0,-.1])
		cylinder(r=get_screw_hole_diameter()/2+backlash,h=get_screw_hole_length()+.11,$fn=20);

		assign(r1=1.0*nut_diameter/2+backlash)
		assign(r2=0.95*nut_diameter/2+backlash)
		assign(r3=1.05*nut_diameter/2+backlash)
		assign(h1=bottom_thickness)
		assign(h2=h1+nut_thickness-0.04*nut_diameter)
		assign(h3=h1+nut_thickness-0.01*nut_diameter)
		assign(h30=h1+nut_thickness)
		assign(h4=h1+nut_thickness+.1*nut_diameter)
		assign(h5=h4+.2*nut_diameter)
		assign(h6=max(h5,height))
        rotate([0,0,360/nut_sides/2])
		rotate_extrude($fn=nut_sides)
		if(bottom_thickness>0)
		polygon(points=[[r1,h1],[r1,h2],[r2,h3],[r2,h4],[r3,h5],[r3,h6+.1],[0,h6+.1],[0,h1]]);
		else
		polygon(points=[[r1,h1-.1],[r1,h30],[0,h30],[0,h1]]);
	
		if(cross_section)
		translate([-1000/2,0,-.1])
		cube([1000,1000,100]);
	}
}
else
for(a=[-45,45])
rotate([0,0,a])
cube([1,10,0.2],center=true);

module create_knurled()
translate([0,0,h1])
difference()
{
	if(part=="simple")
	create_simple_knurled();
	else if(part=="hex")
    hull()
	create_shaped_knurled();
	else if(part=="clamp")
	create_knurled_clamp();
    else if(part=="wing")
    create_wings();
	else
	create_shaped_knurled();

	assign(points=[[get_diameter_2()/2,-.01],[get_diameter_2()/2+1000,1000/2],[get_diameter_2()/2+1000,-.01]])
	if(part!="rounded"&&bottom_thickness!=0.0&&supportless_friendly==1)
	rotate_extrude($fn=60)
	polygon(points);
}

module create_knurled_clamp()
difference()
{
	cylinder(r=(2*knurled_r+get_diameter_2())/2,h=height-h1,$fn=60);

	for(a=[0:get_knurled_n()-1])
	rotate(360/get_knurled_n()*a)
	translate([get_diameter_2()/2+knurled_r,0,-.1])
	cylinder(r=knurled_r,h=height-h1+.2,$fn=30);
}

module create_simple_knurled(fn=4)
assign(n=round(get_knurled_n()/2))
for(a=[0:n-1])
rotate(360/fn/n*(a+.5))
cylinder(r=(2*knurled_r+get_diameter_2())/2,h=height-h1,$fn=fn);

module create_shaped_knurled()
for(a=[0:get_knurled_n()-1])
rotate(360/get_knurled_n()*(a+.5))
translate([get_diameter_2()/2,0,0])
if(part=="rounded"||part=="hex")
hull()
create_knurled_rounded();
else if(part=="cylindrical")
create_knurled_cylindrical();

module create_knurled_rounded()
for(z=[knurled_r,height-h1-knurled_r])
translate([0,0,z])
sphere(r=knurled_r,$fn=20);

module create_knurled_cylindrical()
cylinder(r=knurled_r,h=height-h1,$fn=20);

module create_wings()
assign(len=knurled_r*get_diameter_2()*.7)
linear_extrude(height=height-h1,convexity=20)
hull()
{
    circle(r=get_diameter_2()/2,$fn=60);
        
    for(a=[0:1])
    rotate(360/get_knurled_n()*(a+.5))
    translate([len,0,0])
    circle(r=get_diameter_2()/4,$fn=30);
}

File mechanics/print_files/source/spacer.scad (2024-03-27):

// arduino spacer

//2mm hoch 3,5 innen

$fn=100;

difference() {
  cylinder(d=7, 2);
  translate([0,0,-.1]) cylinder(d=3.5, 3);
}

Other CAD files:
mechanics/print_files/Protection_Foot-Body.stl
mechanics/print_files/tpu-eierhalter-stiftseite.stl
mechanics/print_files/nut_knob_v1_5_1_M4.stl
mechanics/print_files/source/spring-3mm.scad
mechanics/print_files/Box_IntersectionNew.stl
mechanics/print_files/Faucet.stl
mechanics/print_files/penarm-strongerV2.stl
mechanics/print_files/source/toolmount.scad
mechanics/print_files/source/tpu-eierhalter.scad
mechanics/print_files/stepperholderV4.stl

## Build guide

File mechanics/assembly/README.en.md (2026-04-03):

## eggbot77 assembly instructions for the mechanics



In the tradition of a popular manufacturer of kids toys located in the city of Billund, Denmark (whose name we will intentionally omit here for reasons) we have divided the manual in several assembly groups:

## assembly group 1: fixation of the egg

Tools needed: 2 spanners 10mm

Screw the threaded rod (M5) and insert it half way through the [tailstock holder](eb77-eh21_bauteil-01.JPG)
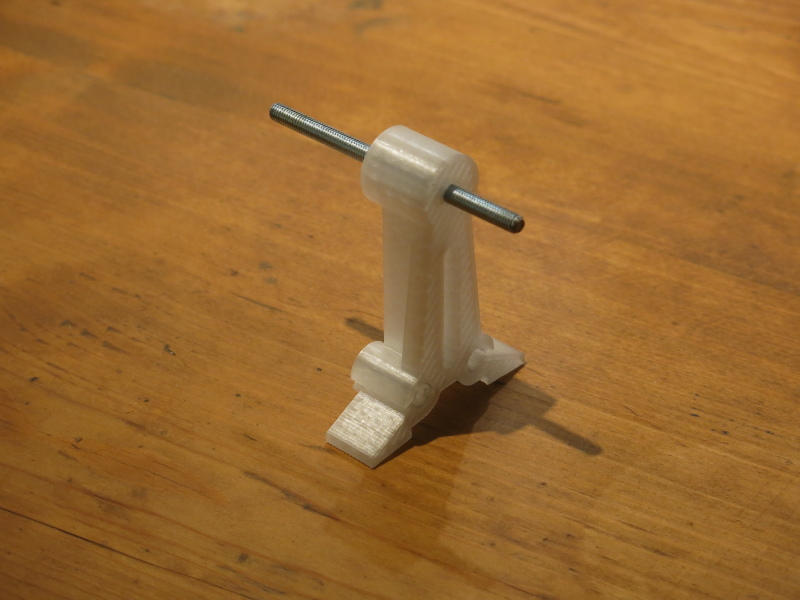
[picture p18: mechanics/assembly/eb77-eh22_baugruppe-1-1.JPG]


Add one of the M5 nuts on the flat(!) side of the tailstock holder
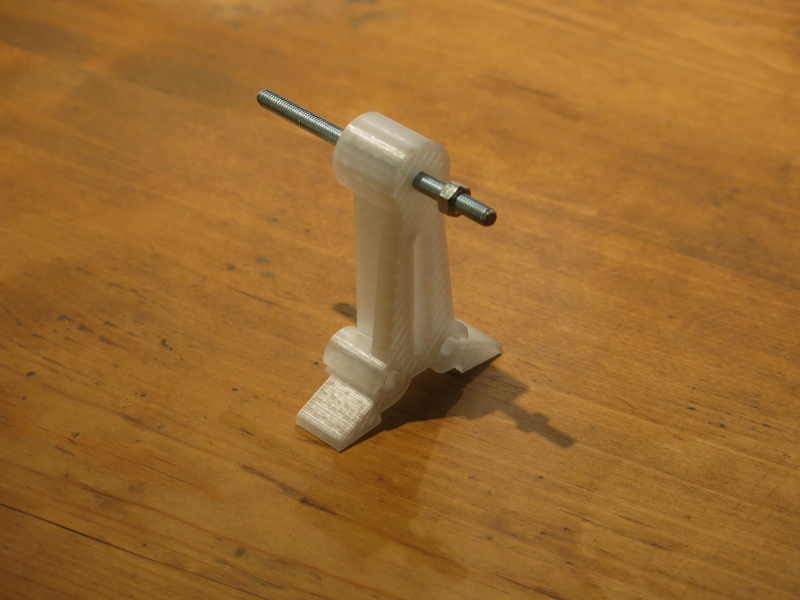
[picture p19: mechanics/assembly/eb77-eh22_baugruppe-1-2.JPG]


Add the bearing (625ZZ) and the second of the M5 nuts to the rod.
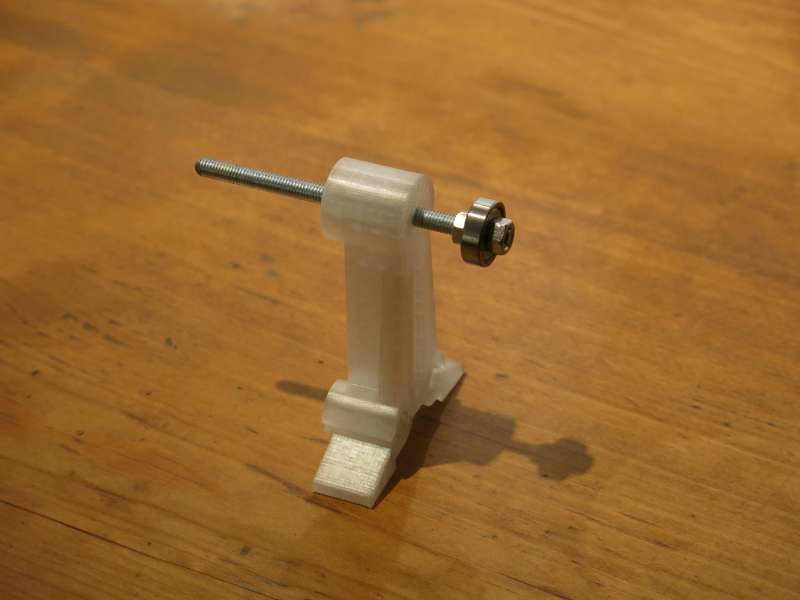
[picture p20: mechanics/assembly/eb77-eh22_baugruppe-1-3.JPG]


Hints: 
* the second nut should be flush with the end of the threaded rod, next to the bearing which should be next to the nut you inserted first
* make sure the two nuts hold the bearing firmly. That will take some artistic degrees of freedom from you eggbot77, though ;)
* now put the [Eierhalter Lagerseite](eb77-eh21_bauteil-03-a.JPG) on the bearing

Now only the [faucet](eb77-eh21_bauteil-02.JPG) is missing - ready is your first assembly group! You're doing great! ;)
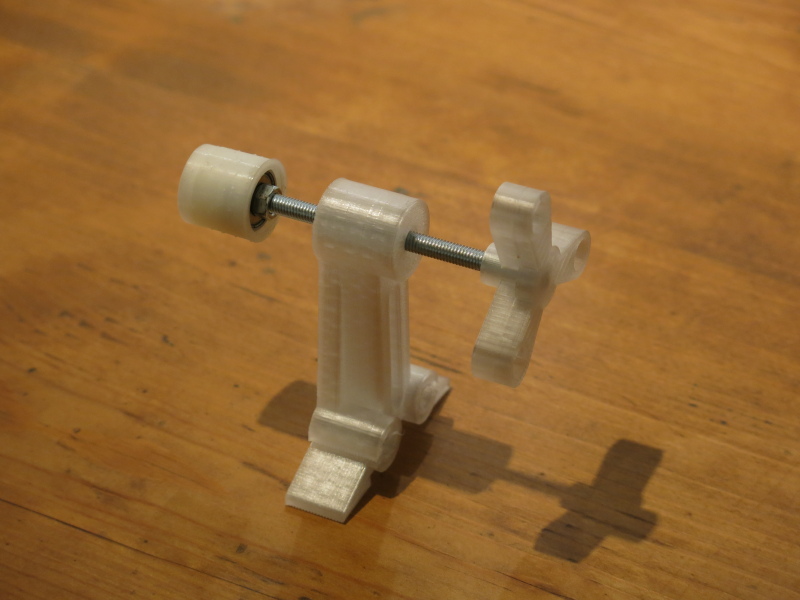
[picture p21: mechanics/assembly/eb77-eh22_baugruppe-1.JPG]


## assembly group 2a: fixation of the pen

Tools needed: none

Don't get a drink just yet - this will be a very quick one.
Insert the M4 bolt into the [nut knob](eb77-eh21_bauteil-04.JPG)
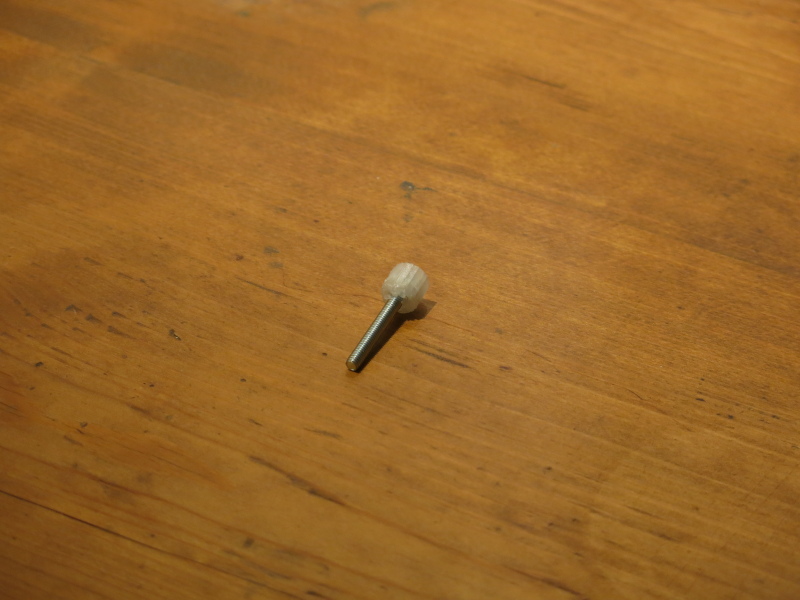
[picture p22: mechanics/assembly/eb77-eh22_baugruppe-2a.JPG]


There you go - assembly group 2a is done, too!

## assembly group 2b: pen holder arm (integrates assembly group 2a)

Tools needed: Allen key 2mm, Phillips head screwdriver medium, Phillips head screwdriver tiny (PH00)

This is going to be a bit trickier. But do not worry. You'll be fine.
Insert the M3x20 bolt with the cylinder head through the hole in the [toolmount](eb77-eh21_bauteil-05.JPG) attaching the [spring](eb77-eh21_bauteil-06.JPG) to it.
Hints: give the following picture a close look and you'll see which of the many ways this could be done is the only correct one.

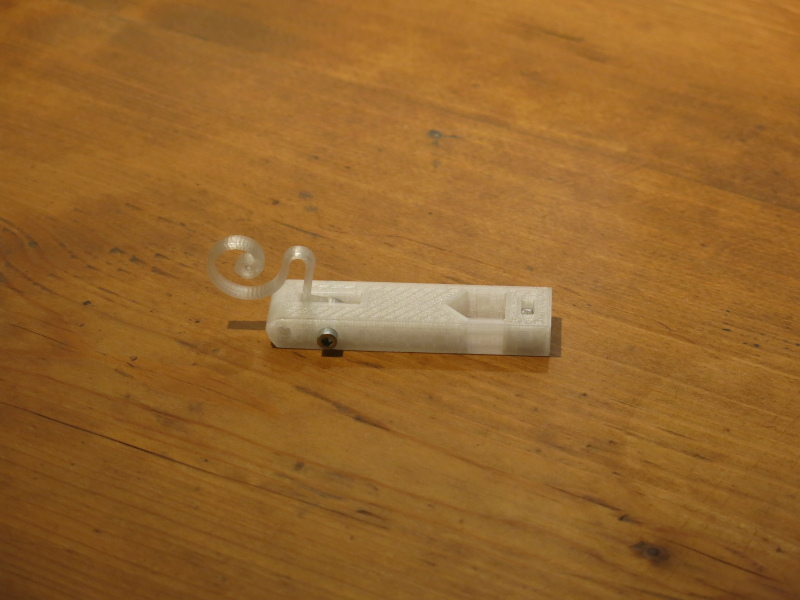
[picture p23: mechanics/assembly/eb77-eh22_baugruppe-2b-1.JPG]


Now take the M3x30 bolt to attach the [penarm](eb77-eh21_bauteil-07.JPG) to the toolmount.
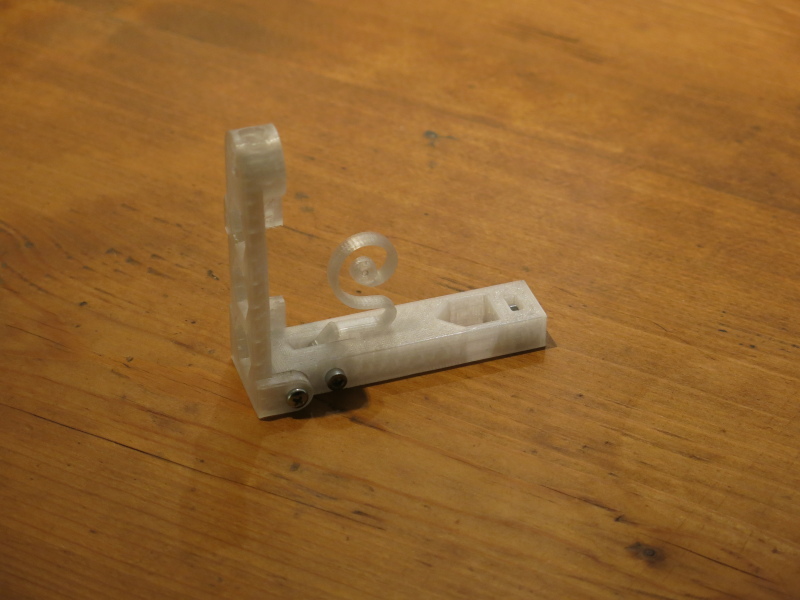
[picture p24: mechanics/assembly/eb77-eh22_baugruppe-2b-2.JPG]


Secure the screw with the lock nut (that's the one with the blue rubber ring).
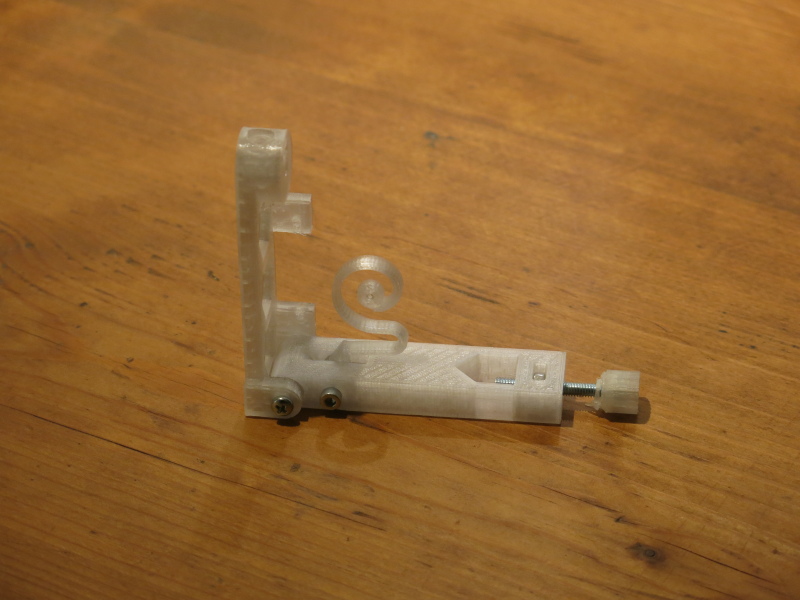
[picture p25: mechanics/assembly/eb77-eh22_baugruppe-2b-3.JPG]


Getting even more tricky now: attach the blue mini servo using the 2 miniature screws. Insert the screws from the servo side so they will rest in the penarm.

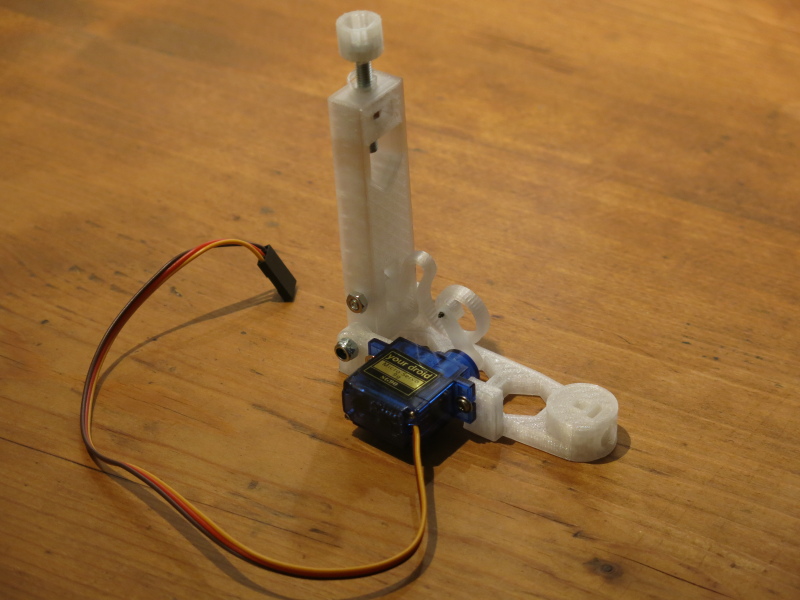
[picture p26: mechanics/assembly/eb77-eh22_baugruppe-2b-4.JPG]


Fix the servo arm with the single 3mm screw.
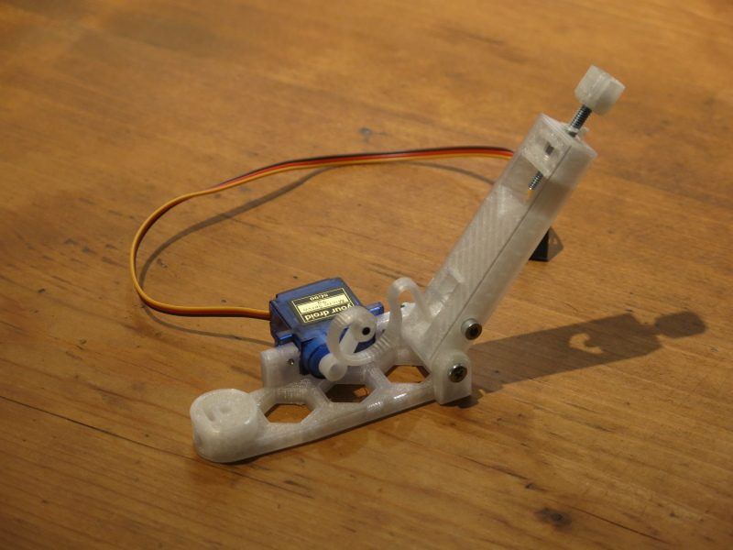
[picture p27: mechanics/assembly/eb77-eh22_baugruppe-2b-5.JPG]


Hint: you might need to re-adjust the angle at which the arm is fixed to the servo later. So don't worry too much about that now.

One more special screw (the smallest one that was provided to you as part of the kit) will fix the open end of the spring to the servo arm. Use the last of the holes inside the arm.


## assembly group 3: PCB holder
That's an easy one again. Use the 4 3mm screws to attach the PCB to the [nema eggbot77 mount/PCB holder](eb77-eh21_bauteil-08.JPG) with the [spacers](eb77-eh21_bauteil-09.JPG).
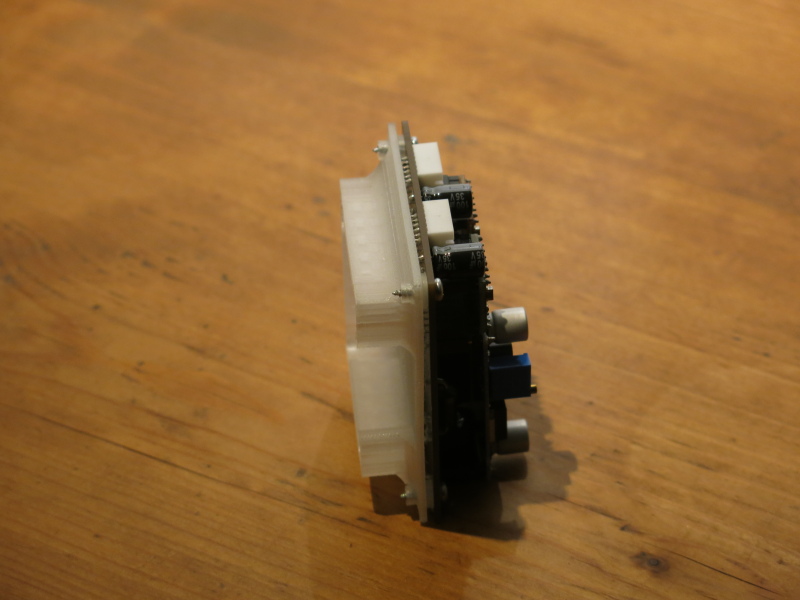
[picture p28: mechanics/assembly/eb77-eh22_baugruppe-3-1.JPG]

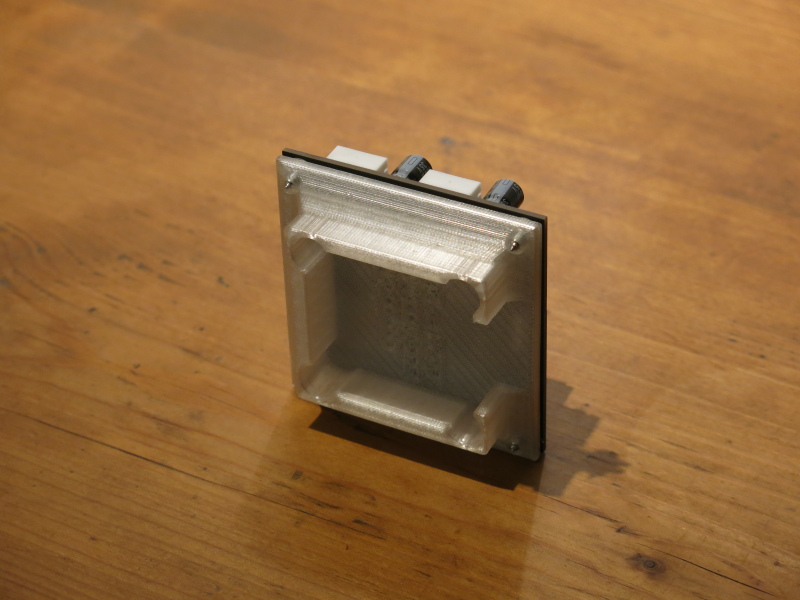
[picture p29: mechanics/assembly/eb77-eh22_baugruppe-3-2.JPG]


## complete assembly: integrates remaining single parts and all assembly groups

Tools needed: Phillips head screwdriver medium

You are now ready to assemble your EggBot77! Take the 2 shorter (!) ones of the 6mm alumiminum rods and put them through the holes of the [box intersecting rods](eb77-eh21_bauteil-10.JPG) which are closed on one side. Now take the 2 remaining rods and put them through the holes of the box that go all the way through.
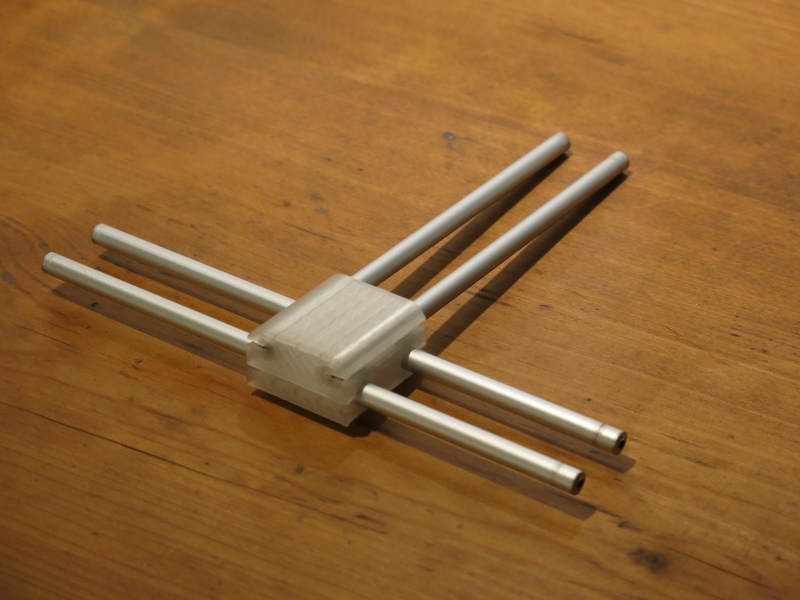
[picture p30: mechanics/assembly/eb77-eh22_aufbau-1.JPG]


Now insert the countersunk M3x20 to the top of the box and secure it with the remaining M3 nut.
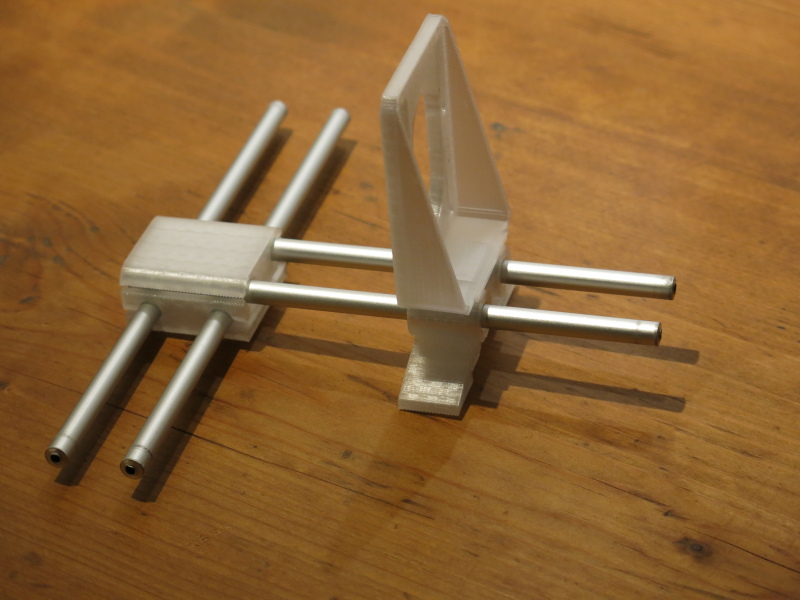
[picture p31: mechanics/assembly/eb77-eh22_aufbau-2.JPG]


Put the [stepperholder for the pen](eb77-eh21_bauteil-11.JPG) (easily identified by its long vertical holes that allow for height adjustments of the stepper - and is one of the improvements of this year's model, BTW) onto the shorter pair of rods.
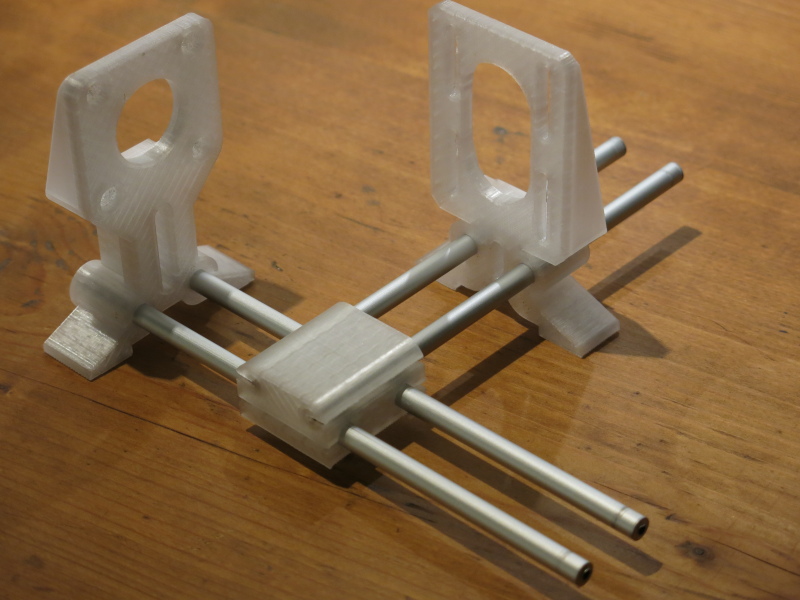
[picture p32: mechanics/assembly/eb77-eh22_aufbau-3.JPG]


The other end of these rods go into the [pen stepper holder foot](eb77-eh21_bauteil-12.JPG).
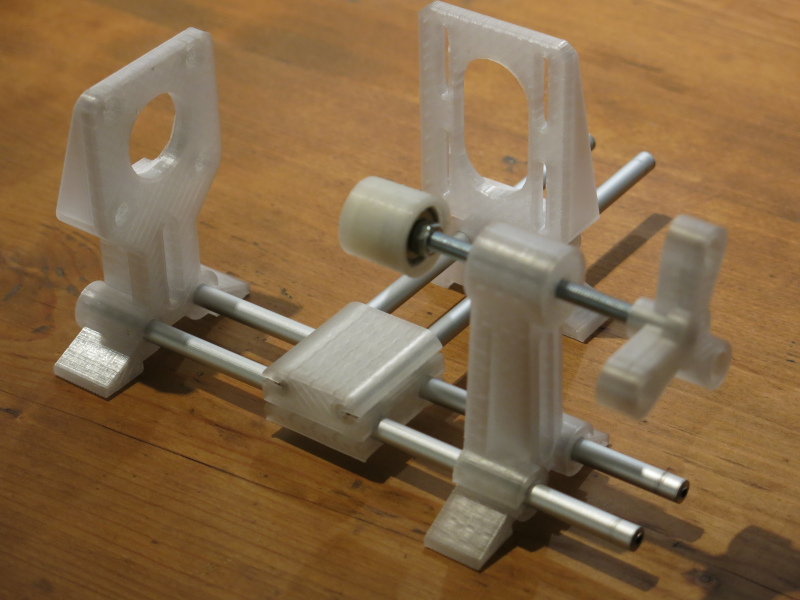
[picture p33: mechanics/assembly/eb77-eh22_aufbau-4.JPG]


The [rotational stepper holder](eb77-eh21_bauteil-13.JPG) goes to the left end of the longer pair of rods; that's when the pen stepper holder is on the far side of the bot. Starting to take shape, isn't it?
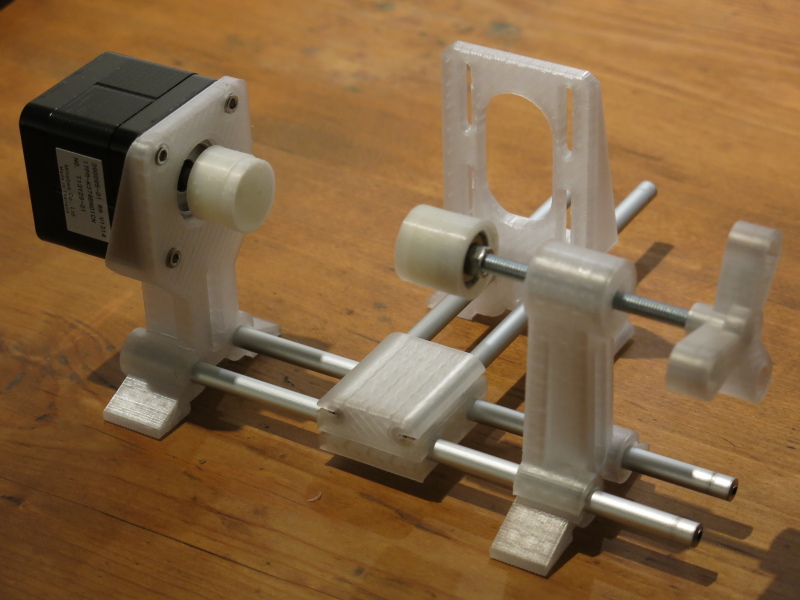
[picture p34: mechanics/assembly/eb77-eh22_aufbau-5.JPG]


Now add the preassembled [assembly group 1](eb77-eh21_baugruppe-1-3.JPG) and the [rotational stepper holder foot](eb77-eh21_bauteil-14.JPG) on the right side of the longer pair of rods.
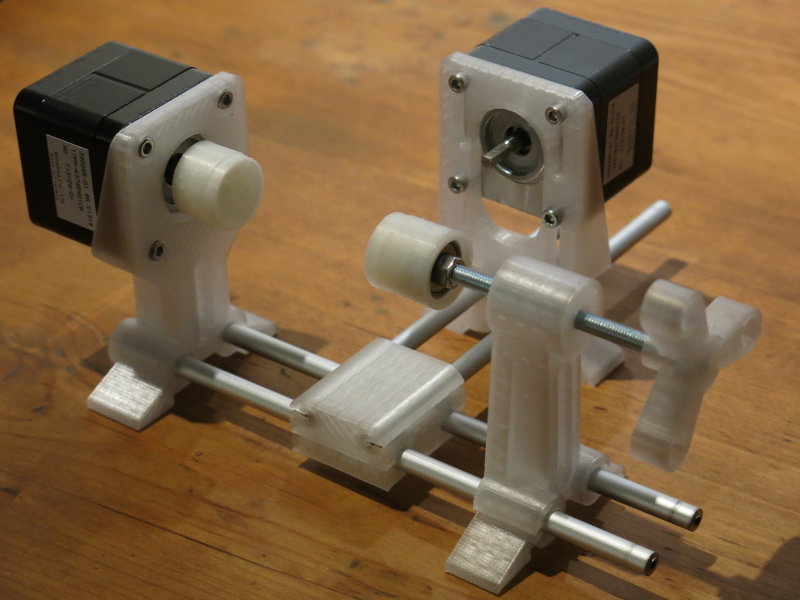
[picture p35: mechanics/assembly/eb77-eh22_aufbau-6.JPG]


Time to add the first stepper (make sure you take the black one)(just kiddin') and the [Eierhalter Stiftseite](eb77-eh21_bauteil-15.JPG) to the assembly.
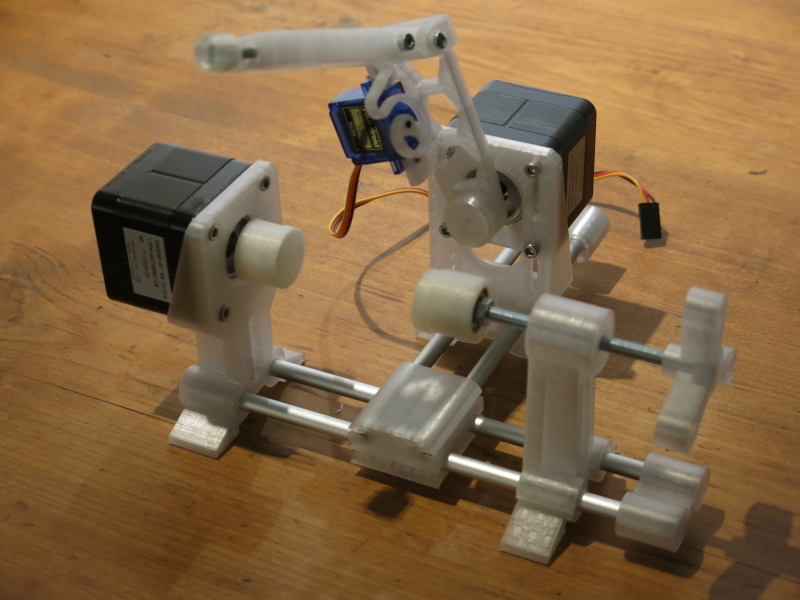
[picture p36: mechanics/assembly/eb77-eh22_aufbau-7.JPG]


Add the second stepper now. You can adjust the height later, just fix it somewhere in the middle for now.
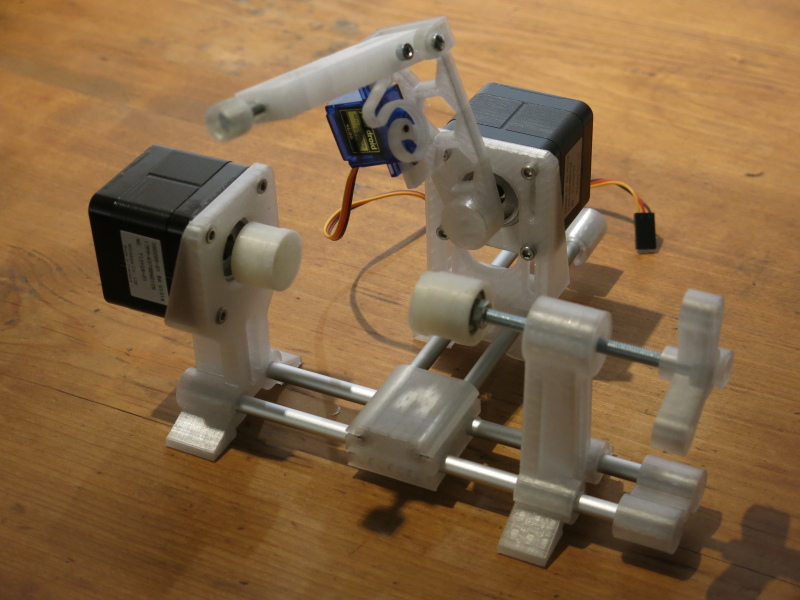
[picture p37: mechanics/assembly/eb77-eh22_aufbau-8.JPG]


Finally: add the preassambled [assembly group 2b](eb77-eh21_baugruppe-2b.JPG) and the [assembly group 3, aka: the PCB](eb77-eh21_baugruppe-3.JPG) and you're done with the mechanics part - congrats!

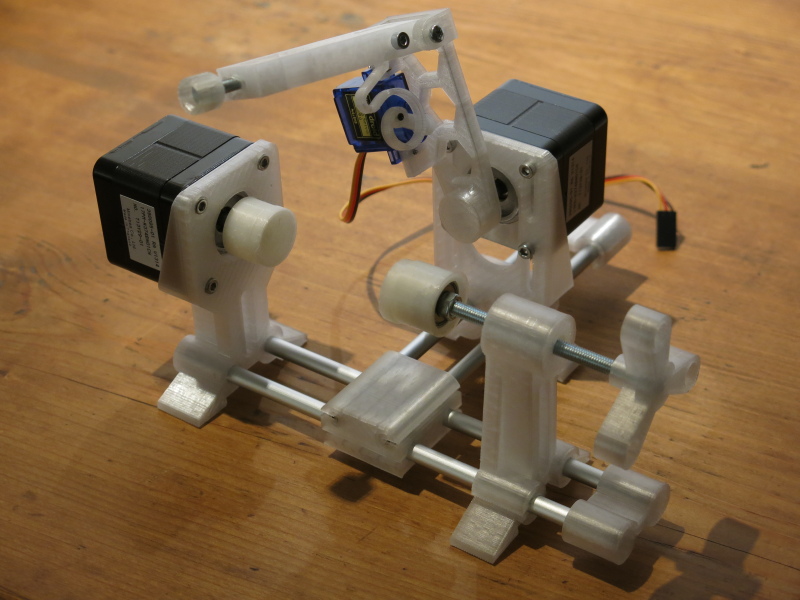
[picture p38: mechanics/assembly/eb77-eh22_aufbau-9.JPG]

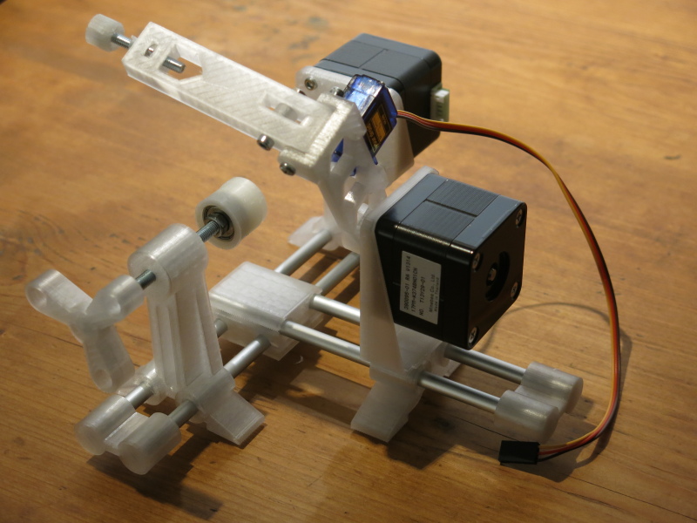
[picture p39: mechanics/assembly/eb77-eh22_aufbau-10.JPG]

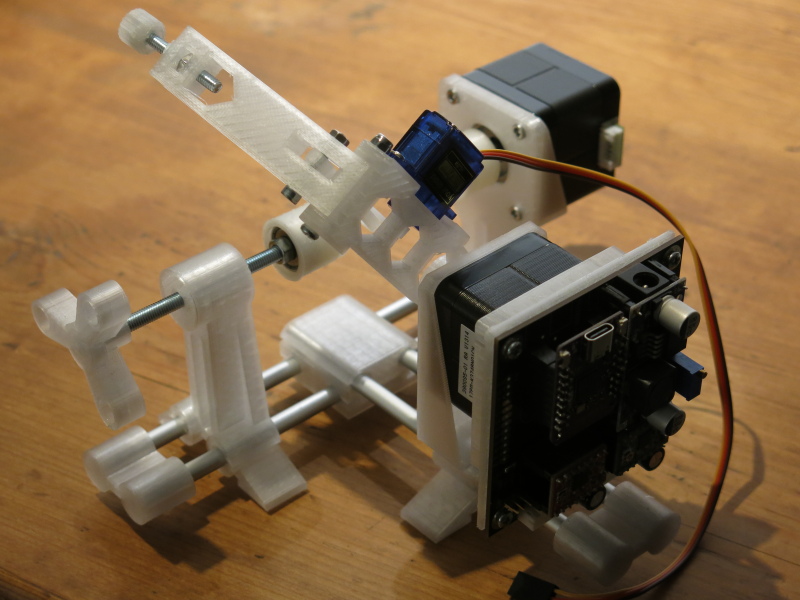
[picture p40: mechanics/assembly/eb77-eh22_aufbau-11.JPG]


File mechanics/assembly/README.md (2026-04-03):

## eggbot77 Montageanleitung für die Mechanik



In Anlehnung an einen bekannten Hersteller von Kinderspielzeug aus der dänischen Stadt Billund (dessen Namen wir hier aus Gründen bewusst weglassen) haben wir die Anleitung in mehrere Baugruppen unterteilt:

## Montagegruppe 1: Fixierung für des Ei

Benötigte Werkzeuge: 2 Gabelschlüssel 8 mm

Schraube die Gewindestange (M5) bis zur Hälfte durch den [Reitstockhalter](eb77-eh21_bauteil-01.JPG)


Eine der M5-Muttern auf der flachen(!) Seite des Reitstockhalters anbringen


Bring' das Lager (625ZZ) und die zweite der M5-Muttern an der Stange an.


Hinweise: 
* Die zweite Mutter sollte mit dem Ende der Gewindestange bündig sein und direkt neben dem Lager, das sich neben der zuerst eingesetzten Mutter befinden sollte.
* Stell' sicher, dass die beiden Muttern das Lager festhalten. Das nimmt dem EggBot77 allerdings einige künstlerische Freiheitsgrade ;)
* Jetzt noch den [Eierhalter Lagerseite](eb77-eh21_bauteil-03-a.JPG) auf das Lager aufstecken

Jetzt fehlt nur noch der [Wasserhahn](eb77-eh21_bauteil-02.JPG) - fertig ist Deine erste Baugruppe! Das machst du toll! ;)


## Baugruppe 2a: Fixierung des Stiftes

Benötigte Werkzeuge: keines

Hol' Dir noch nichts zu trinken - das geht ganz schnell.
Führe die M4-Schraube in den [Griff](eb77-eh21_bauteil-04.JPG)


Na bitte - Baugruppe 2a ist auch fertig!

## Baugruppe 2b: Stifthalterarm (integriert Baugruppe 2a)

Benötigte Werkzeuge: Innensechskantschlüssel 2,5 mm, Kreuzschlitzschraubendreher mittel, Kreuzschlitzschraubendreher klein (PH00)

Das wird jetzt ein bisschen kniffliger. Aber keine Sorge. Du schaffst das schon.
Stecke die Zylinderkopfschraube M3x20 durch das Loch in der [Werkzeughalterung](eb77-eh21_bauteil-05.JPG) und befestige die [Feder](eb77-eh21_bauteil-06.JPG) daran.
Hinweis: Schau' Dir das folgende Bild genau an, dann wirst Du sehen, welche der vielen Möglichkeiten die einzig richtige ist. Sichere die Schraube mit der normalen M3-Mutter.


Nimm nun die M3x30-Schraube, um den [Stiftarm](eb77-eh21_bauteil-07.JPG) an der Werkzeughalterung zu befestigen. Sichere die Schraube mit der Stoppmutter (das ist die Mutter mit dem blauen Gummiring).


Als Nächstes setzt Du die M4-Mutter in die Aussparung der Werkzeughalterung ein und schraubst die Baugruppe 2a hinein.


Jetzt wird es noch etwas kniffliger: Befestige das blaue Mini-Servo mit den 2 Miniaturschrauben. Setze die Schrauben von der Servoseite her ein, so dass das Ende im Stiftarm sitzt.


Befestige den Servoarm mit der einzelnen 3 mm-Schraube.


Hinweis: Möglicherweise musst Du den Winkel, in dem der Arm am Servo befestigt ist, später nachjustieren. Mach' Dir jetzt sich also nicht zu viele Gedanken darüber.

Eine weitere Spezialschraube (die kleinste Schraube, die Du als Teil des Bausatzes erhalten hast) wird das offene Ende der Feder am Servoarm befestigen. Benutze das letzte der Löcher im Inneren des Arms.


## Baugruppe 3: Platinenhalter

Benötigte Werkzeuge: Innensechskantschlüssel 2,5 mm

Das wird jetzt wieder einfach. Befestige die Platine mit den letzten 4 der M3x8 mm-Schrauben am [Platinenhalter](eb77-eh21_bauteil-08.JPG) mit den [Abstandhaltern](eb77-eh21_bauteil-09.JPG)




## Vollständiger Zusammenbau: integriert die restlichen Einzelteile und alle Baugruppen

Benötigte Werkzeuge: Kreuzschlitzschraubendreher mittel, Innensechskantschlüssel 2,5 mm

Du bist nun bereit, Deinen EggBot77 zusammenzubauen! Nimm die 2 kürzeren (!) der 6 mm Aluminiumstangen und stecke sie in die Löcher der [zentralen Box](eb77-eh21_bauteil-10.JPG), die auf einer Seite verschlossen sind. Nun nimmst du die 2 verbleibenden Stangen und steckst sie durch die durchgängigen Löcher der Box.


Steck' den [Stepperhalter für den Stift](eb77-eh21_bauteil-11.JPG) (leicht zu erkennen an den langen vertikalen Löchern, die eine Höhenverstellung des Steppers ermöglichen) auf das kürzere Stangenpaar.


Der [Rotationsstepperhalter](eb77-eh21_bauteil-13.JPG) kommt an das linke Ende des längeren Stangenpaars; dann befindet sich der Stiftstepperhalter auf der anderen Seite des Bots. Langsam nimmt er Gestalt an, nicht wahr?


Füge nun die vormontierte [Baugruppe 1](eb77-eh22_baugruppe-1.JPG) und den [Schutz](eb77-eh22_bauteil-14.JPG) auf der rechten Seite des längeren Stangenpaares hinzu.


Es ist an der Zeit, den ersten Schrittmotor (achte darauf, dass Du den mit dem Zahnrad nimmst) und den [Eierhalter für die Motorseite](eb77-eh21_bauteil-15-a.JPG) hinzuzufügen.



Füge jetzt den zweiten Stepper hinzu. Du kannst die Höhe später anpassen, aber fixiere ihn erst einmal irgendwo in der Mitte.


Zum Schluss fügst du die vormontierte [Baugruppe 2b](eb77-eh22_baugruppe-2b-5.JPG) und die [Baugruppe 3, alias: die Platine](eb77-eh22_baugruppe-3-2.JPG) hinzu und bist mit dem Mechanikteil fertig - Glückwunsch!





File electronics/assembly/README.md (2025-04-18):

## eggbot77 Aufbauanleitung



Hinweis: Die Stiftleisten JP1 und JP4 werden für den Easterhegg-Workshop nicht verwendet und sind dafür gedacht, falls jemand Erweiterungen anbringen möchte oder die Platine außerhalb der Osterzeit für andere Projekte verwenden will.

Wir haben versucht den Aufbau der Platine so detailiert wie nötig mit vielen Bildern zu beschreiben, so dass auch am Lötkolben wenig erfahrene Bastler zurecht kommen. Eine Einführung ins grundsätzliche Löten von Elektronikbauteilen enthält diese Anleitung nicht. Wenn es anfängt nach gebratenem Hühnchen zu riechen, hälst du den Lötkolben verkehrt herum ;-)

### Lötbrücke SJ7 schließen

Dadurch wird das 3,3V PWM Signal des ESP32s direkt an den Servo duchgegeben. Der SG90 "Micro Servo 9g" kommt normalerweise mit dem 3,3V Pegeln zurecht. Solltest du einen anderen Servo mit 5V PWM verwenden wollen, kannst du diesen Schritt überspringen und stattdessen Q1 und R1 einlöten.

Für den Easterhegg-Workshop empfehlen wir SJ7 zu schließen.

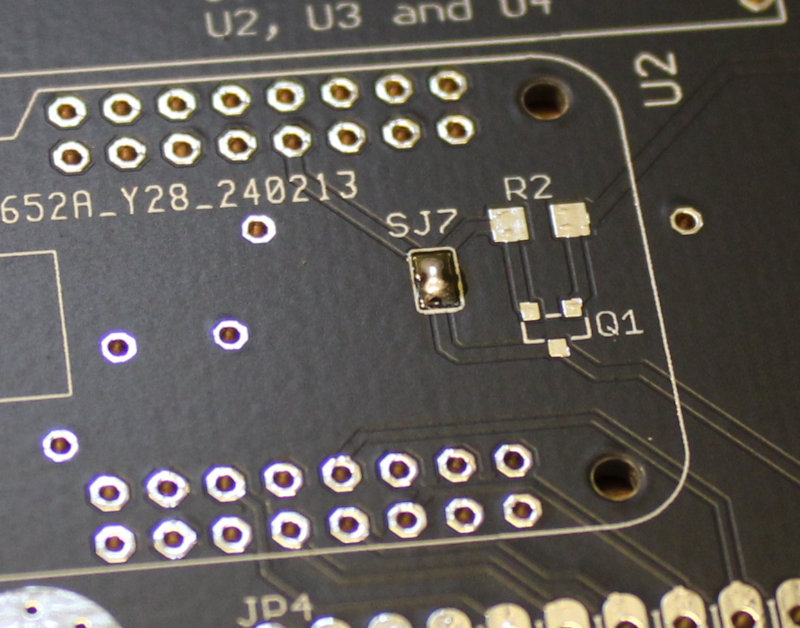
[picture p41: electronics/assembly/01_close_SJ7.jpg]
solder jumper SJ7 closed to enable 3.3V PWM signals to servo


### Lötbrücken für microstepping schließen

Die Eggbot77 firmware geht davon aus, dass am A4988 Treiber 1/16 Microstepping aktiv ist (alle drei Lötbrücken MS1-MS3 an beiden Treibern geschlossen). Wenn Du einen anderen Schrittmotor, als den beigelegten Minebea 17PM-K374BN01CN verwenden willst oder den Schrittmotorstrom messen und einstellen willst, solltest du die Lötbrücken zunächst offen lassen und erst ganz am Ende schließen.

Für den Easterhegg-Workshop empfehlen wir alle 6 Lötbrücken zu schließen.

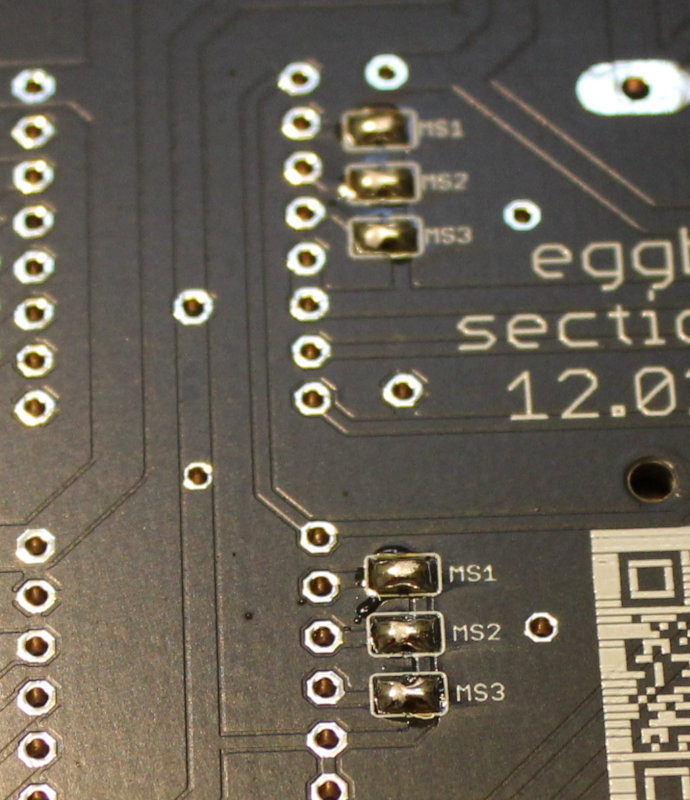
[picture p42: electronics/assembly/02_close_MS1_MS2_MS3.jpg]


### Buchsenleisten vorbereiten

Wir müssen uns kürzere Buchsenleisten aus den großen 1x20 Buchsenleisten zuschneiden. Beim Abknipsen wird unweigerlich ein Pin zerstört, daher empfiehlt es sich genau mittig auf dem Pin zu schneiden und die entstehende Kante noch einmal nachzubearbeiten.

Es werden vorerst vier Stück 1x8 Buchsenleiste gebraucht (siehe übernächstes Bild)

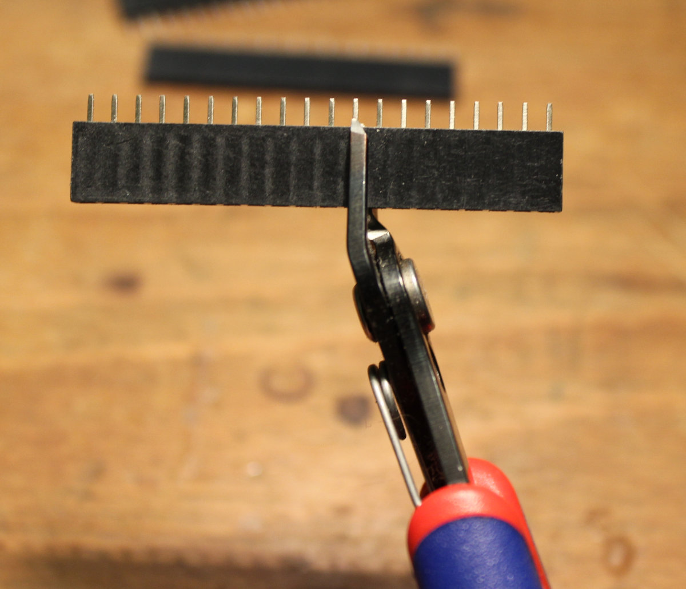
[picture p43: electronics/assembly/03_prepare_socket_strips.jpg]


### Vorbereitete Komponenten

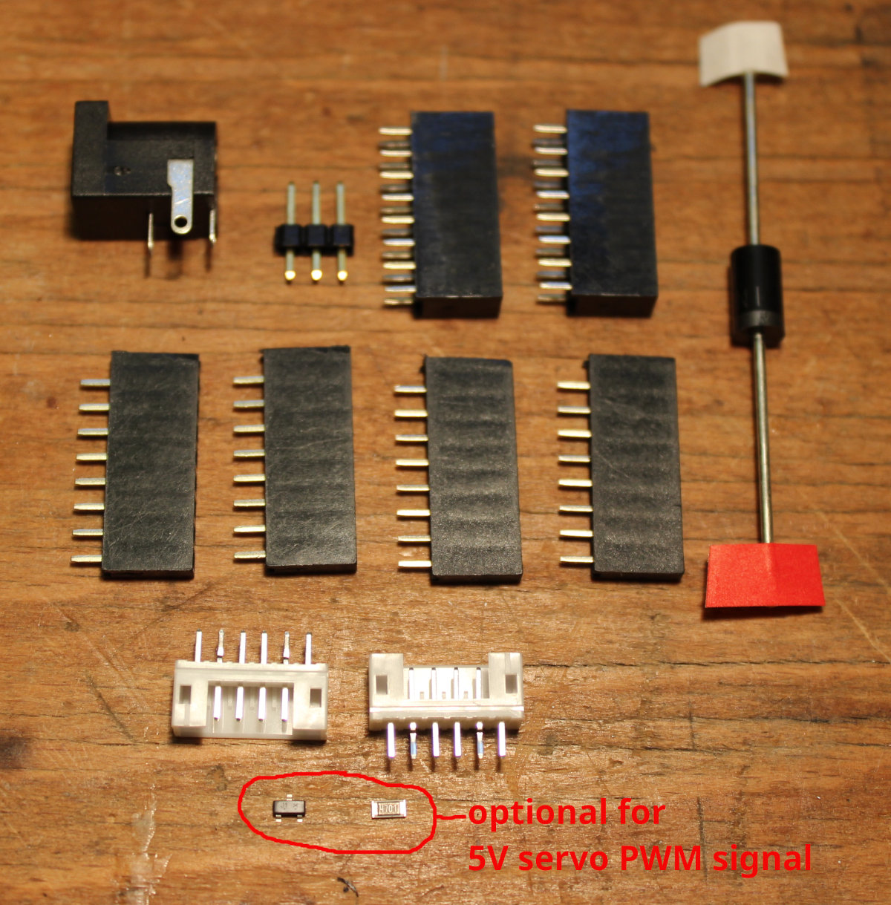
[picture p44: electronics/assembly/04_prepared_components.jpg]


### Buchsenleiste für U2

Die zwei 2x8 Buchsenleisten (fertig konfektioniert) einsetzen und umgedreht auf eine ebene Fläche legen.
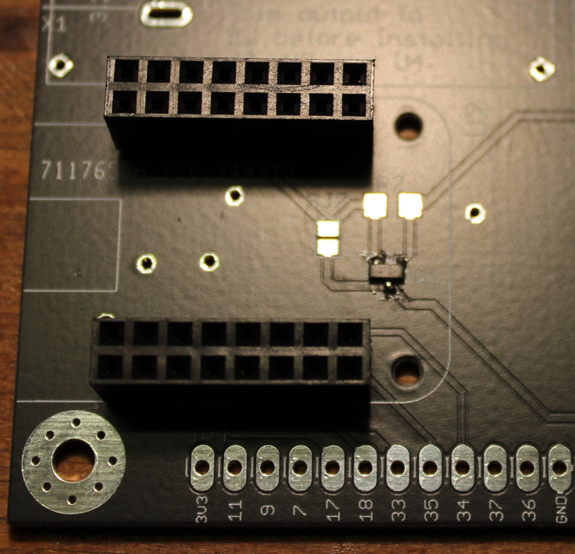
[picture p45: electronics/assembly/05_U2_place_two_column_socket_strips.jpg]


Dann zuerst jeweils 1 Pin anlöten, nochmals den korrekten Sitz prüfen und dann alle Pins durchlöten.
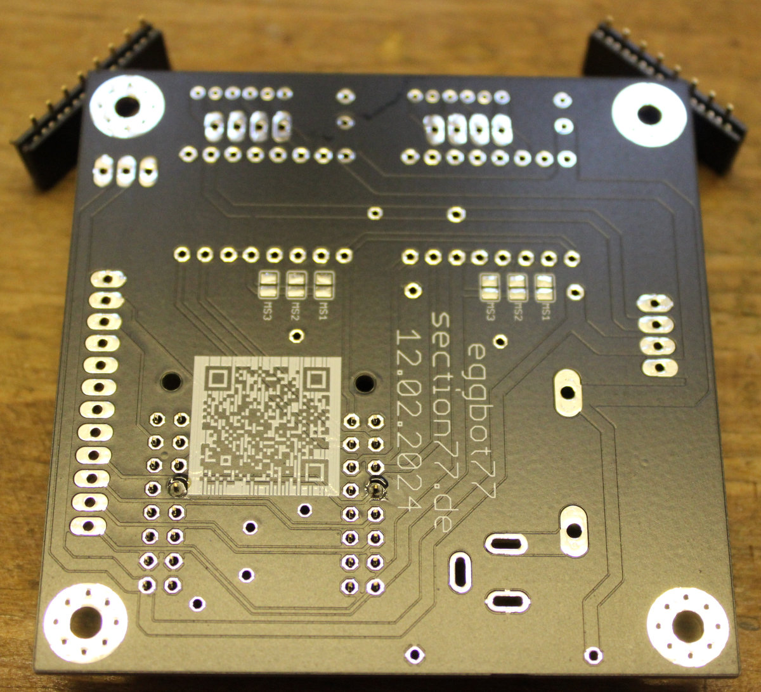
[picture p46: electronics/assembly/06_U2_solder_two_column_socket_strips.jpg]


### Buchsenleiten für U3 und U4

Es empfiehlt sich als Hilfsmittel einen A4988 Treiber einzustecken um die Buchsenleisten in Position zu halten. Die JST Stecker X2 und X3 klemmen in den Löchern und können parallel eingesetzt werden.
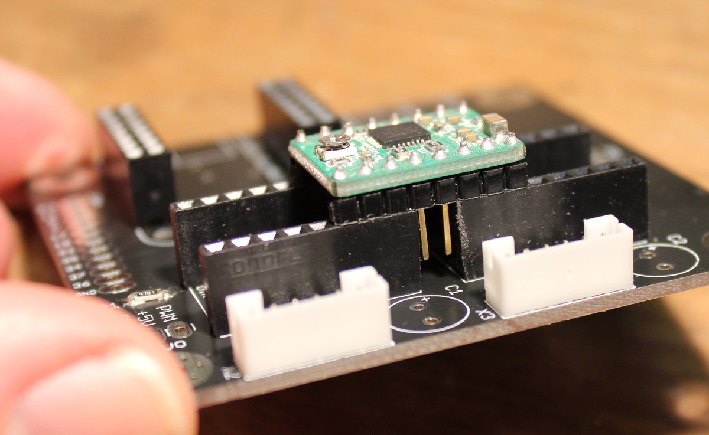
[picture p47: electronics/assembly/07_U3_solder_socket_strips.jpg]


Auf dem Bild sieht man die durchgelöteten Buchsenleisten für U2, U3, U4, X2 und X3
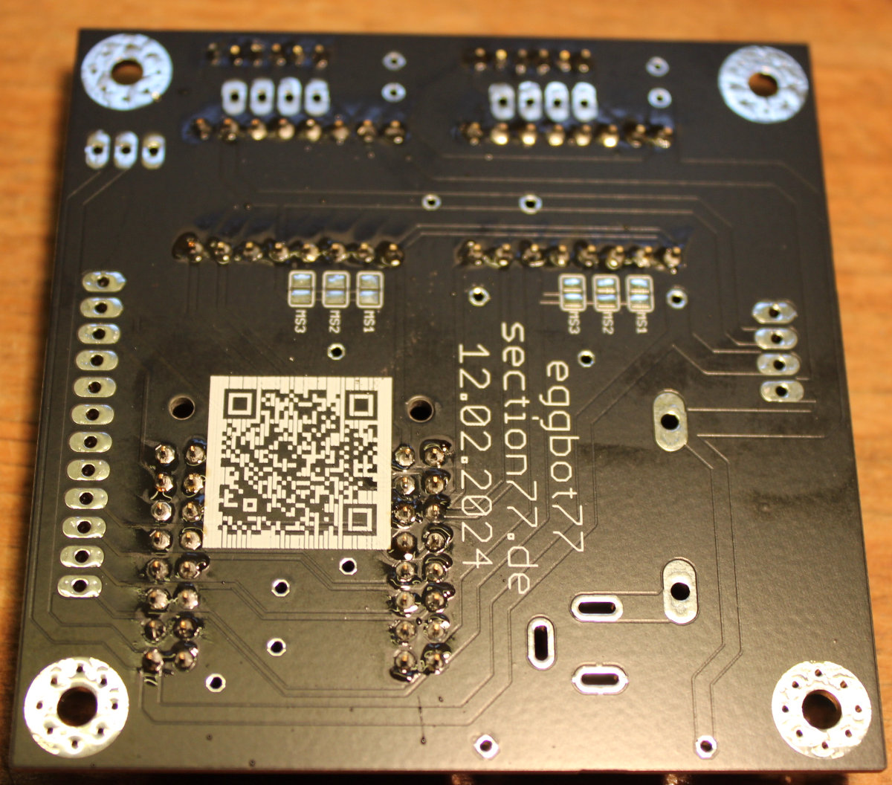
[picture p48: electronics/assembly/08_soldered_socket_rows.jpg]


### Schottky Diode D1 einlöten

Beinchen mit einer Spitzzange passend abwinkeln
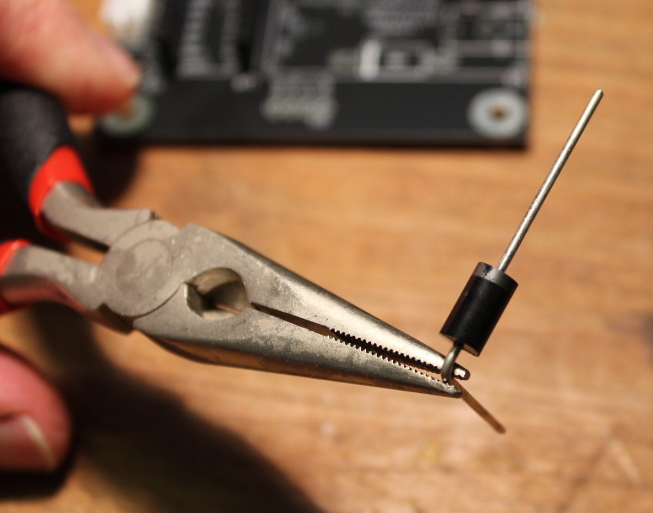
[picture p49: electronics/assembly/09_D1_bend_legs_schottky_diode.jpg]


Nach dem Platzieren auf die passende Länge abschneiden. Die Beinchen vor dem Löten abzuschneiden ist ein wichtiger Schritt weil ansonsten zu viel Wärme abfließt, die dann an der Lötstelle fehlt. Für diesen und den nächsten Schritt (X1 einlöten) kann es notwendig sein den Lötkolben, bei Verwendung mit bleifreiem Lot, kurzzeitig auf 400°C zu stellen.

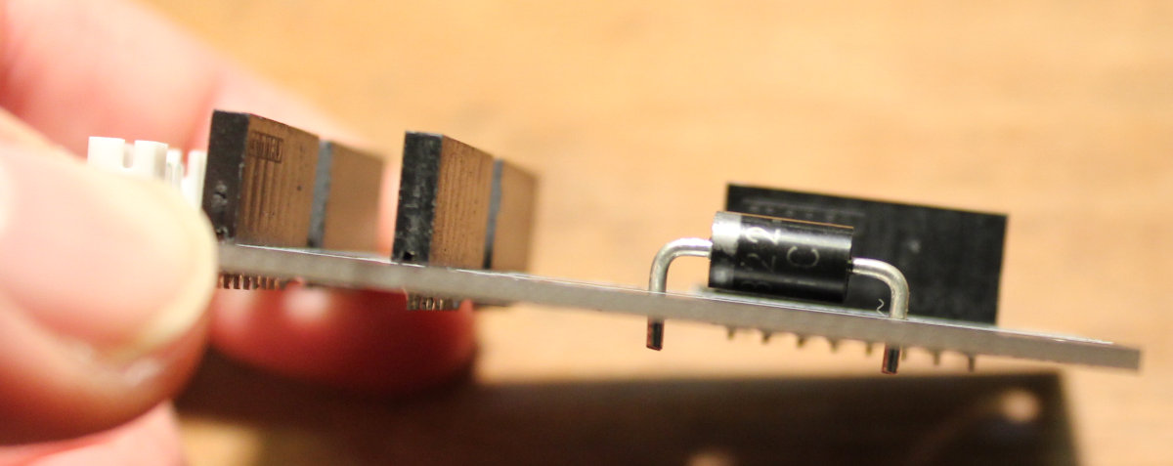
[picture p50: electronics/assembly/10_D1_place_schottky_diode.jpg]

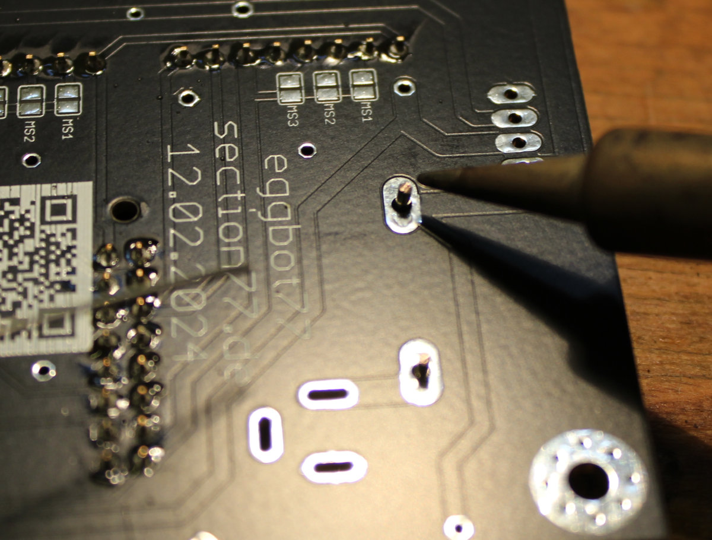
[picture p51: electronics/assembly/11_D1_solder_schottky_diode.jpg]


### Hohlbuchse X1 einlöten
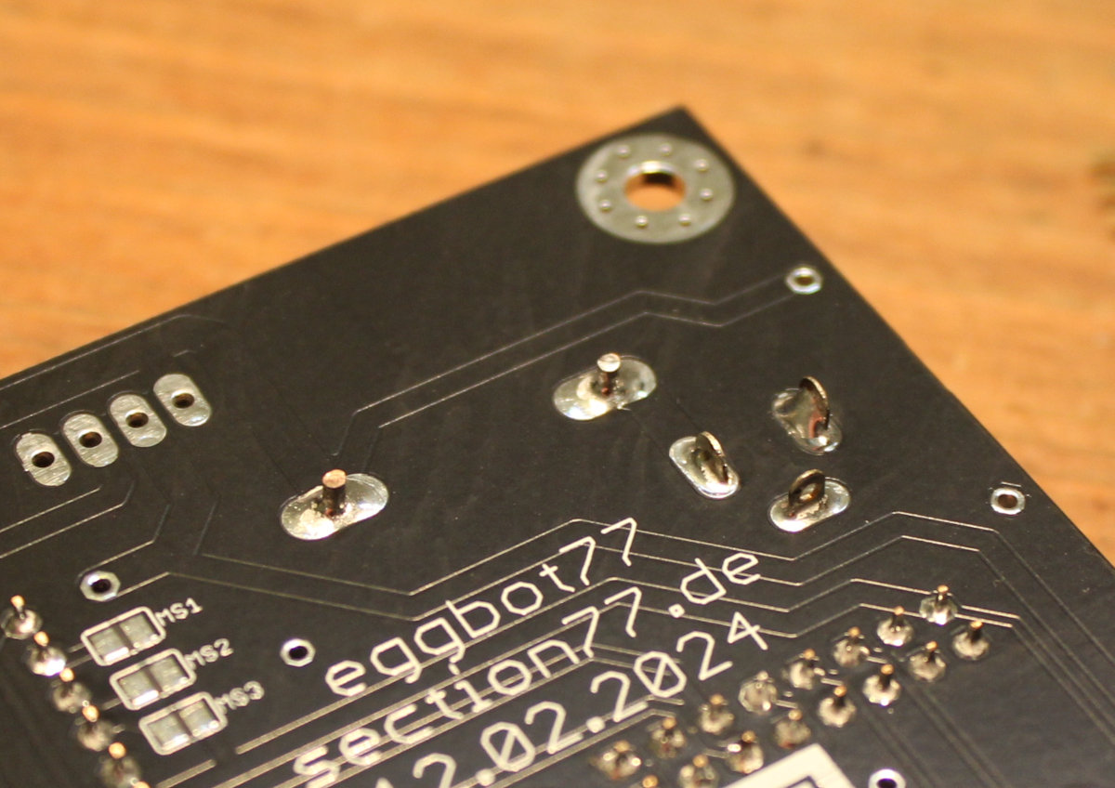
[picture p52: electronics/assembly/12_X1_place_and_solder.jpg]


### Kondensatoren vorbereiten

Wichtig: Auf korrekte Ausrichtung achten. Das lange Beinchen am Kondensator muss zum + Symbol auf der Platine, der weiße Strich mit "-" am Kondensator zeigt zum Rand.

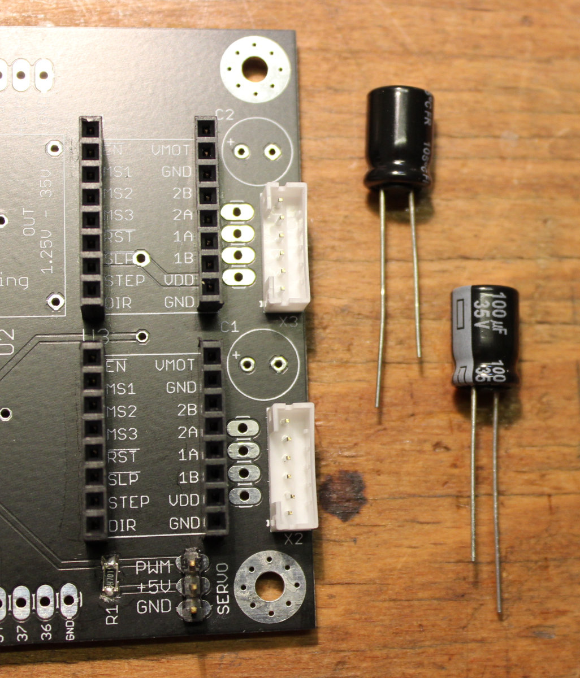
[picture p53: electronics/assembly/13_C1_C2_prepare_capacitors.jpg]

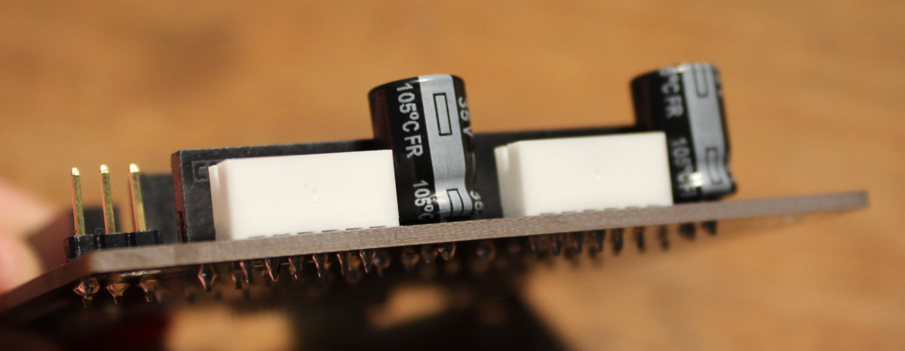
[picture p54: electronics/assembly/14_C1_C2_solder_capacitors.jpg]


### Sifte und Buchsen für U1 vorbereiten

Wie vorher gezeigt mit dem Seitenschneider 4 Stifte und 4 Buchsen von den großen Leisten abschneiden.

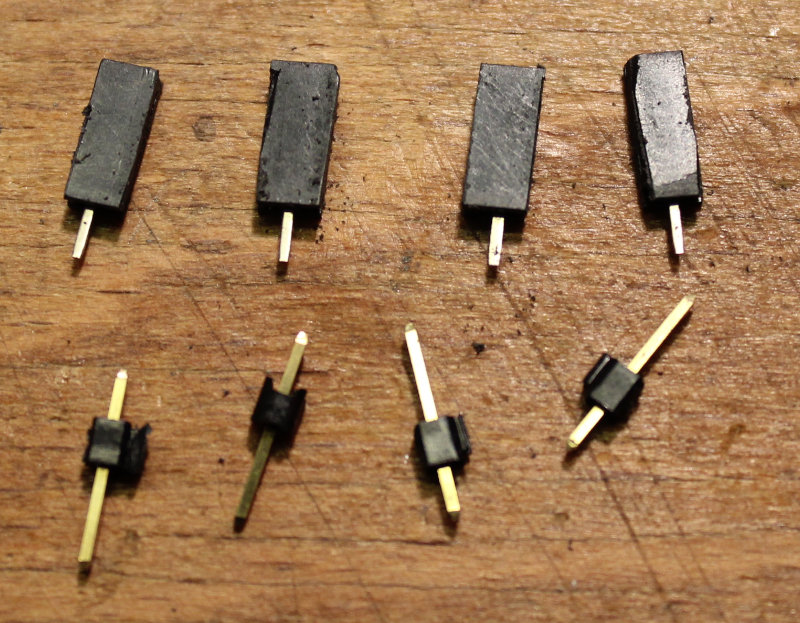
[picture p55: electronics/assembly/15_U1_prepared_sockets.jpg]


### Stifte an U1 anlöten

Es empfiehlt sich drei Stifte ausgerichtet in die bestehenden Buchsenleisten einzustecken und auf der LM2596 Platine anzulöten. Dies hilft bei der senkrechten Ausrichtung der Pins. Anschließend um 180° drehen und verbleibenden Pin anlöten.

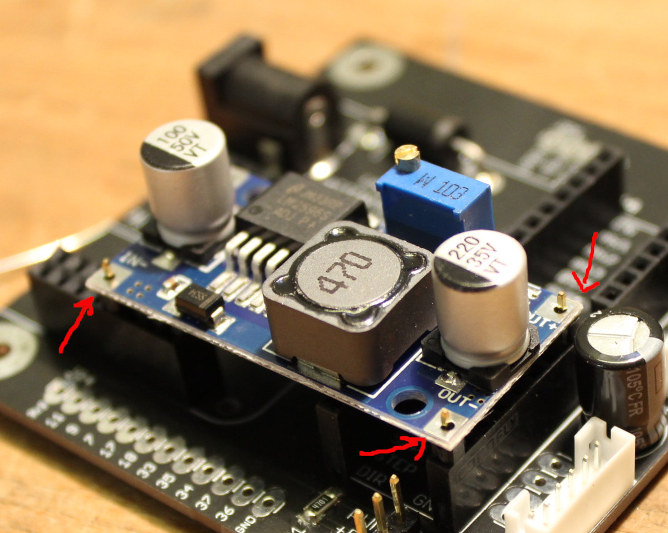
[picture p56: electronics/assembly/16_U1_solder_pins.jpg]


### Buchsen an U1 anlöten

Auch hier ist es empfehlenswert die 4 vorher zugeschnittenen Buchsen ausgerichtet auf die Stifte aufzusetzen, dann die Platine zu wenden und dann die 4 Buchsen anzulöten.

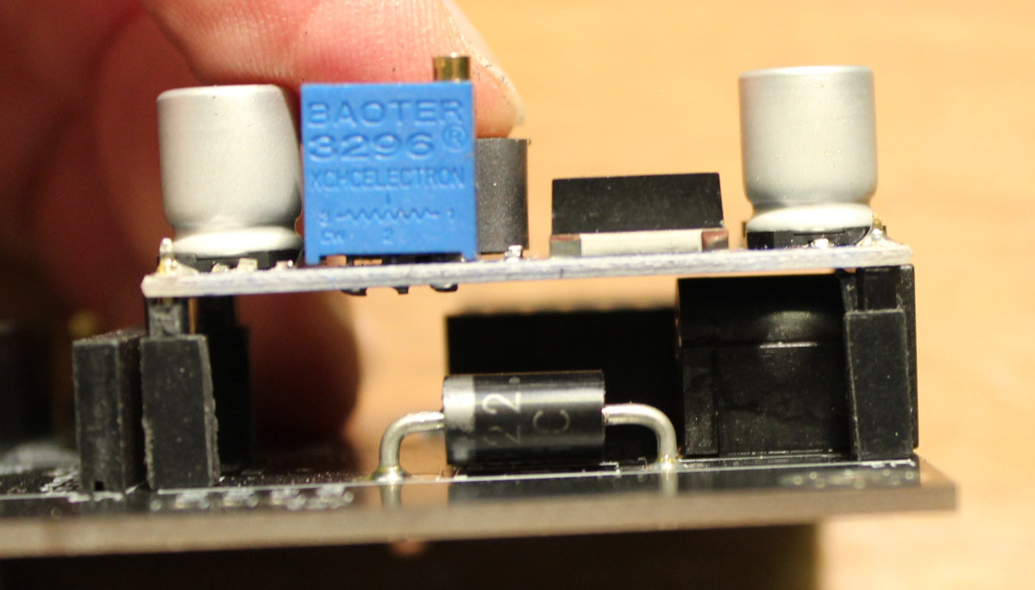
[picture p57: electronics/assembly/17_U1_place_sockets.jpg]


### Ausgangsspannung an U1 einstellen

Auf korrekte Ausrichtung des Moduls achten: Der blaue Trimmer muss zum Rand der Platine zeigen. Die Ausrichtung der Aufschrift "IN+, OUT+" usw. muss zur Ausrichtung der unteren Platine "JP1" passen. Siehe auch nächstes Bild.

**Achtung:** Die A4988 Treiber(U3 und U4) sowie der ESP32(U1) wird zerstört, wenn sie eingebaut sind und die Platine mit 12V betrieben wird, bevor die Ausgangsspannung am Spannungsregler U1 eingestellt wurde.

Daher vor dem Einstecken des Netzteils und dem ersten Einschalten nochmal darauf achten, dass U2, U3 und U4 nicht aufgesteckt sind. Siehe auch das nachfolgende Bild:



Der Trimmer (roter Pfeil) muss ca. 12.5 mal gegen den Uhrzeigersinn gedreht werden, um die 5V am Ausgang einzustellen. Die Ausgangsspannung fängt erst nach ca. 7 Linksdrehungen an, sich zu ändern, also bitte nicht vorzeitig aufgeben...



### Module aufstecken

Nun Netzteil ausstecken und die Module U2, U3 und U4 aufstecken.

An U2 (dem ESP32) muss die USB-C Buchse "nach links" zum Rand zeigen.

An den A4988 Modulen muss Enable/En zur Beschriftung auf der Platine passen. Der Trimmer (mit dem Kreuzschlitz) zeigt dann in Richtung der Servo Pfostenleiste (auch auf dem übernächsten Bild zu sehen).

Die Beschriftung auf der Rückseite der A4988 Platine steht dann auf dem Kopf, davon darf man sich nicht abschrecken lassen.

Wichtig ist, dass der rot umkreiste "Enable" Pin zum "En" auf der Platine passt.



### Servo und Schrittmotoren anstecken

Die orange Leitung am SG90 muss zum Pin "PWM" ausgerichtet sein. Andere Servos können andere Farbkodierungen haben.

Die Schrittmotoren mit den Leitungen verbinden, die Ferrite (die schwarzen Röhrchen) zu der Platine hin.

X3 (im Bild der obere der beiden Anschlüsse) bewegt den Stift, X2 (naja - das ist dann wohl der untere der beiden :D ) rotiert das Ei.



### Hardware mit Testprogramm prüfen

Wenn man den ESP32 das erste Mal mit der arduino IDE programmieren möchte, muss man ihn in den DFU Modus (Device Firmware Upgrade Mode) bringen:
* Taster 0 am ESP32 drücken und festhalten (untere linke Ecke, mit "0" beschriftet)
* Taster Reset (linke obere Ecke, mit "RST" beschriftet) drücken
* Taster 0 noch kurz halten und dann loslassen

Quelle: https://www.wemos.cc/en/latest/tutorials/s2/get_started_with_arduino_s2.html

Es empfiehlt sich zuerst das [hardware_test Arduino Projekt](../../firmware/hardware_test/hardware_test.ino)
zu programmieren, um die korrekte Funktion der Komponenten vorab zu testen.

Der Servo läuft dabei langsam von der Minimumposition zur Maximumposition, beide Schrittmotoren drehen mit unterschiedlichen Geschwindigkeiten abwechselnd in beide Richtungen und die blaue onboard LED blinkt mit 1Hz.

Wenn das funktioniert, steht dem Programmieren der richtigen [EggBot77 firmware](../../firmware/EggBot77/EggBot77.ino) zur Kommunikation mit dem Inkscape plugin nichts mehr im Wege.

Weiter mit der [Installation des Inkscape Plugins](../../inkscape_1.x_extension/README.md)

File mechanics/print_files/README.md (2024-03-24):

This directory contains the files for 3d printing in stl format.

Most of the files have been gathered from the interwebz:

[Vladislav Trigubovich](https://www.thingiverse.com/trigubovich/) has created the [base design](https://www.thingiverse.com/thing:2422393/). The following files have been copied from that (licensed under CC BY-4.0):
- Box_Intersecting_Rods.stl
- Pen_Stepper_Holder_Foot.stl
- Pen_Stepper_Holder-V2.stl
- Tailstock_Holder.stl
- Rotational_Stepper_Holder_Foot.stl
- Rotational_Stepper_Holder.stl
- Faucet.stl

[schuetzi99](https://www.thingiverse.com/schuetzi99) has provided a remix which replaces the bought metal spring with a printed one and fitting toolmount and penarm (licensed under CC BY-NC-SA-4.0):
- toolmount.stl ([OpenSCAD](OpenSCAD/toolmount.scad))
- spring-3mm.stl (modified by me to allow for a 3mm bolt, [OpenSCAD](OpenSCAD/spring-3mm.scad))
- penarm-stronger.stl (modified by me to strengthen the arms holding the servo, [OpenSCAD](OpenSCAD/penarm-stronger.scad))
- nema-eggbot77-mount.stl ([OpenSCAD](OpenSCAD/nema-eggbot77-mount.scad)) (schuetzi99's version was for Arduino Uno; I have modified this to fit our own ESP32-based PCB; bruder-jo made the fit more universal to allow for different variants of nema17 steppers and also allows for more tolerance of different printers).
schuetzie99 also provided his files in OpenSCAD format which made modifications dead simple :)

[Smuk3D](https://www.thingiverse.com/smuk3d) has designed a knob for the M4 bolt that fixes the pen:
- nut_knob_v1_5_1_M4.stl ([OpenSCAD](OpenSCAD/nut_knob_v1_5_1_M4.scad))

I have designed two new files for holding the egg (print in TPU) replacing the original PLA ones using suction cups:
- tpu-eierhalter-lagerseite.stl ([OpenSCAD](OpenSCAD/tpu-eierhalter.scad); set "lagerseite=true") (thx to bruder-jo for improving printability!)
- tpu-eierhalter-stiftseite.stl ([OpenSCAD](OpenSCAD/tpu-eierhalter.scad); set "lagerseite=false")

Optionally you can also print the pads for the feet (print in TPU):
- tpu-pad-16x15.stl (print 8)
- tpu-pad-19x15.stl (print 2)

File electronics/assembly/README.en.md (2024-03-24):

## eggbot77 assembly instructions



Note: The pin headers JP1 and JP4 are not used for the Easterhegg workshop and are intended for use if someone wants to add extensions or use the board for other projects outside the Easter period.

We have tried to describe the structure of the board in as much detail as necessary with lots of pictures, so that even less experienced hobbyists can manage with a soldering iron. These instructions do not contain an introduction to the basic soldering of electronic components. If it starts to smell like fried chicken, you're holding the soldering iron wrong ;-)

### Close solder bridge SJ7

This sends the 3.3V PWM signal from the ESP32 directly to the servo. The SG90 "Micro Servo 9g" normally copes with the 3.3V level. If you want to use a different servo with 5V PWM, you can skip this step and solder Q1 and R1 instead.

For the Easterhegg workshop we recommend closing SJ7.

solder jumper SJ7 closed to enable 3.3V PWM signals to servo

### Close solder jumpers for microstepping

The Eggbot77 firmware assumes that microstepping is active on the A4988 driver 1/16 (all three solder jumpers MS1-MS3 on both drivers closed). If you want to use a stepper motor other than the included Minebea 17PM-K374BN01CN or want to measure and set the stepper motor current, you should leave the solder bridges open at first and only close them at the very end.

We recommend closing all 6 solder bridges for the Easterhegg workshop.



### Preparing the socket strips

We have to cut shorter socket strips from the large 1x20 socket strips. One pin will inevitably be destroyed when clipping off, so it is advisable to cut exactly in the middle of the pin and to rework the resulting edge.

For the time being, four 1x8 socket strips are needed (see picture after next)



### Prepared components



### Socket strip for U2

Insert the two 2x8 socket strips (pre-assembled) and place them upside down on a flat surface.


Then solder on 1 pin at a time, check again that it is correctly seated and then solder through all the pins.


### Socket strips for U3 and U4

It is recommended to insert an A4988 driver as an aid to hold the socket strips in position. The JST connectors X2 and X3 are clamped in the holes and can be used in parallel.


The picture shows the soldered socket strips for U2, U3, U4, X2 and X3


### Solder in Schottky diode D1

Angle the legs appropriately with needle-nose pliers


After placement, cut to the appropriate length. Cutting off the legs before soldering is an important step because otherwise too much heat will flow away, which will then be missing at the soldering point. For this and the next step (soldering X1), it may be necessary to briefly set the soldering iron to 400°C when using lead-free solder.




### Solder in hollow socket X1


### Prepare capacitors

Important: Ensure correct alignment. The long leg on the capacitor must point to the + symbol on the circuit board, the white line with "-" on the capacitor points to the edge of the PCB.




### Prepare pins and sockets for U1

Cut off 4 pins and 4 sockets from the large strips using the side cutters as shown above.



### Solder the pins to U1

We recommend inserting three pins into the existing socket strips and soldering them to the LM2596 board. This helps with the vertical alignment of the pins. Then rotate by 180° and solder the remaining pin.



### Solder the sockets to U1

Here, too, it is advisable to place the 4 previously cut sockets on the pins, then turn the board over and solder the 4 sockets.



### Setting the output voltage at U1

Ensure that the module is correctly aligned: The blue trimmer must point towards the edge of the circuit board. The alignment of the label "IN+, OUT+" etc. must match the alignment of the lower circuit board "JP1". See also the next picture.

**Attention:** The A4988 drivers (U3 and U4) and the ESP32 (U1) will be destroyed if they are installed and the board is operated with 12V before the output voltage has been set on the voltage regulator U1.

Therefore, before plugging in the power supply unit and switching on for the first time, make sure that U2, U3 and U4 are not plugged in. See also the following figure:



The trimmer (red arrow) must be turned anticlockwise approx. 12.5 times to set the 5V at the output. The output voltage only starts to change after approx. 7 counterclockwise turns, so please do not give up prematurely...



### Plug in the modules

Now unplug the power supply unit and plug in the modules U2, U3 and U4.

On U2 (the ESP32), the USB-C socket must point "left" to the edge.

On the A4988 modules, Enable/En must match the labeling on the board. The trimmer (with the cross slot) then points in the direction of the servo pin header (also shown in the picture after next).

The labeling on the back of the A4988 board is then upside down, so don't let this put you off.

It is important that the "Enable" pin circled in red matches the "En" on the board.



### Connecting the servo and stepper motors

The orange wire on the SG90 must be aligned with the "PWM" pin. Other servos may have different color coding.

Connect the stepper motors to the cables, the ferrites (the black tubes) to the circuit board.

X3 (the top one of the two connectors on the picture) moves the pen, X2 (well - that would be the bottom one of the two, then :D ) rotates the egg.



### Check hardware with test program

If you want to program the ESP32 with the arduino IDE for the first time, you have to put it into DFU mode (Device Firmware Upgrade Mode):
* Press and hold button 0 on the ESP32 (lower left corner, labeled "0")
* Press the Reset button (top left corner, labeled "RST")
* Hold button 0 briefly and then release it

Make S2 boards into Device Firmware Upgrade (DFU) mode.

* Hold on Button 0
* Press Button Reset
* Release Button 0 When you hear the prompt tone on usb reconnection

Source: https://www.wemos.cc/en/latest/tutorials/s2/get_started_with_arduino_s2.html

It is recommended to first program the [hardware_test Arduino project](../../firmware/hardware_test/hardware_test.ino)
in order to test the correct function of the components in advance.

The servo runs slowly from the minimum position to the maximum position, both stepper motors rotate at different speeds alternately in both directions and the blue onboard LED flashes at 1Hz.

If this works, nothing stands in the way of programming the correct [EggBot77 firmware](../../firmware/EggBot77/EggBot77.ino) for communication with the Inkscape plugin.

Continue with the [Installation of the Inkscape plugin](../../inkscape_1.x_extension/README.md)

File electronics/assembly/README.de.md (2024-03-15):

## eggbot77 Aufbauanleitung



Hinweis: Die Stiftleisten JP1 und JP4 werden für den Easterhegg-Workshop nicht verwendet und sind dafür gedacht falls jemand Erweiterungen anbringen möchte oder die Platine außerhalb der Osterzeit für andere Projekte verwenden will.

Wir haben versucht den Aufbau der Platine so detailiert wie nötig mit vielen Bildern zu beschreiben, so dass auch am Lötkolben wenig erfahrene Bastler zurecht kommen. Eine Einführung ins grundsätzliche Löten von Elektronikbauteilen enthält diese Anleitung nicht. Wenn es anfängt nach gebratenem Hühnchen zu riechen, hälst du den Lötkolben verkehrt herum ;-)

### Lötbrücke SJ7 schließen

Dadurch wird das 3,3V PWM Signal des ESP32s direkt an der Servo duchgegeben. Der SG90 "Micro Servo 9g" kommt normalerweise mit dem 3,3V Pegeln zurecht. Solltest du einen anderen Servo mit 5V PWM verwenden wollen, kannst du diesen Schritt überspringen und stattdessen Q1 und R1 einlöten.

Für den Easterhegg-Workshop empfehlen wir SJ7 zu schließen.

solder jumper SJ7 closed to enable 3.3V PWM signals to servo

### Lötbrücken für microstepping schließen

Die Eggbot77 firmware geht davon aus, dass am A4988 Treiber 1/16 Microstepping aktiv ist (alle drei Lötbrücken MS1-MS3 geschlossen). Wenn Du einen anderen Schrittmtor, als den beigelegten Minebea 17PM-K374BN01CN verwenden willst oder den Schrittmotorstrom messen und einstellen willst, solltest du die Lötbrücken offen alssen und erst ganz am Ende schließen.

Für den Easterhegg-Workshop empfehlen wir alle 6 Lötbrücken zu schließen.



### Buchsenleisten vorbereiten

Wir müssen uns kürzere Buchsenleisten aus den großen 1x20 Buchsenleisten zuschneiden. Beim Abknipsen wird unweigerlich ein Pin zerstört, daher empfiehlt es sich genau mittig auf dem Pin zu schneiden und die entstehende Kante noch einmal nachzubearbeiten.

Es werden vorerst vier Stück 1x8 Buchsenleiste gebraucht (siehe übernächstes Bild)



### Vorbereitete Komponenten



### Buchsenleiste für U2

Die zwei 2x8 Buchsenleisten (fertig konfektioniert) einsetzen und umgedreht auf eine ebene Fläche legen.


Dann zuerst jeweils 1 Pin anlöten, nochmals den korrekten Sitz prüfen und dann alle Pins durchlöten.


### Buchsenleiten für U3 und U4

Es empfiehlt sich als Hilfmittel einen A4988 Treiber einzustecken um die Buchsenleisten in Position zu halten. Die JST Stecker X2 und X3 klemmen in den Löchern und können parallel eingesetzt werden.


Auf dem Bild sieht man die durchgelöteten Buchsenleisten für U2, U3, U3, X2 und X3


### Schottky Diode D1 einlöten

Beinchen mit einer Spitzzange passend abwinkeln


Nach dem Platzieren auf die passende Länge abschneiden. Die Beinchen vor dem Löten abzuschneiden ist ein wichtiger Schritt weil ansonsten zu viel Wärme abfließt, die dann an der Lötstelle fehlt. Für diesen und den nächsten Schritt (X1 einlöten) kann es notwendig sein den Lötkolben, bei Verwendung mit bleifreiem Lot, kurzzeitig auf 400°C zu stellen.




### Hohlbuchse X1 einlöten


### Kondensatoren vorbereiten

Wichtig: Auf korrekte Ausrichtung achten. Das lange Beinchen am Kondensator muss zum + Symbol auf der Platine, der weiße Strich mit "-" am Kondensator zeigt zum Rand.




### Sifte und Buchsen für U1 vorbereiten

Wie vorher gezeigt mit dem Seitenschneider 4 Stifte und 4 Buchsen von den großen Leisten abschneiden.



### Stifte an U1 anlöten

Es empfiehlt sich drei Stifte ausgerichtet in die bestehenden Buchsenleisten einzustecken und auf der LM2596 Platine anzulöten. Dies hielft bei der senkrechten Ausrichtung der Pins. Anschließend um 180° drehen und verbleibenden Pin anlöten.



### Buchsen an U1 anlöten

Auch hier ist es empfehlenswert die Vier vorher zugeschnittenen Buchsen ausgerichtet auf die Stifte aufzusetzen, dann die Platine zu wenden und dann die 4 Buchsen anzulöten.



### Ausgangsspannung U1 einstellen

Auf korrekte Ausrichtung von U2 achten: Der blaue Trimmer muss zum Rand der Platine zeigen, Die Ausrichtung der Aufschrift "IN+, OUT+" usw. muss zur Ausrichtung der unteren Platine "JP1" passen. Siehe auch nächstes Bild.

**Achtung:** Die A4988 Treiber U3 und U4 sowie der ESP32 wird zerstört, wenn sie eingebaut und die Platine mit 12V eingeschaltet wird, bevor die Ausgangsspannung am Spannungsregler U1 eingestellt wurde.

Daher vor dem Einstecken des Netzteils und dem ersten Einschalten nochmal darauf achten, dass U2, U3 und U4 nicht aufgesteckt sind. Siehe auch das nachfolgende Bild:



Der Trimmer (roter Pfeil) muss ca. 12.5 mal gegen den Uhrzeigersinn gedreht werden, um die 5V am Ausgang einzustellen. Die Ausgangsspannung fängt erst nach ca. 7 Linksdrehungen an sich zu ändern, also bitte nicht vorzeitig aufgeben...



### Module aufstecken

Nun Netzteil ausstecken und die Module U2, U3 und U4 aufstecken.

An U2 (dem ESP32) muss die USB-C Buchse an den Rand zeigen.

An den A4988 Modulen muss Enable/En zur Beschriftung auf der Platine passen, der Trimmer (mit dem Kreuzschlitz) zeigt dann in Richtung der Servo Pfostenleiste (auch auf dem übernächsten Bild zu stehen).

Die Beschriftung auf der Rückseite der A4988 Platine steht dann auf dem Kopf, davon darf man sich nicht abschrecken lassen.

Wichtig ist, dass der rot umkreiste "Enable" Pin zum "En" auf der Platine passt-



### Servo und Schrittmotoren anstecken

Die orange Leitung am SG90 muss zur Platine "PWM" ausgerichtet sein. Andere Servos können andere Farbkodierungen haben.

Die Schrittmotoren mit den Leitungen verbinden, die Feritte zu der Platine hin.



### Hardware Testprogramm flashen

Wenn man den ESP32 das erste Mal mit der arduino IDE flashen möchte, muss man ihn in den DFU Modus (Device Firmware Upgrade) bringen:
* Taster 0 am ESP32 drücken und festhalten (untere linke Ecke unter dem USB-C Stecker)
* Taster Reset (linke obere Ecke) drücken
* Taster 0 noch kurz halten und dann loslassen

Quelle: https://www.wemos.cc/en/latest/tutorials/s2/get_started_with_arduino_s2.html

Es empfiehlt sich zuerst das Arduino Projekt ../../firmware/hardware_test/hardware_ino
zu flashen, um die korrekte Funktion der Komponenten vorab zu testen.

Der Servo läuft dabei langsam von der Minimumposition zur Maximumposition, beide Schrittmotoren drehen mit unterschiedlichen Geschwindigkeiten abwechselnd in beide Richtungen und die blaue onboard LED blinkt mit 1Hz.

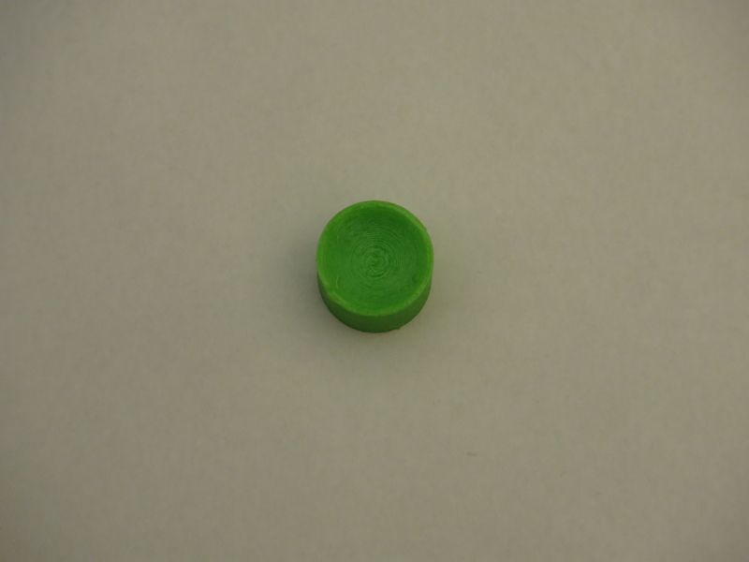
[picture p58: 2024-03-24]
mechanics/assembly/eb77-eh21_bauteil-03-a.JPG

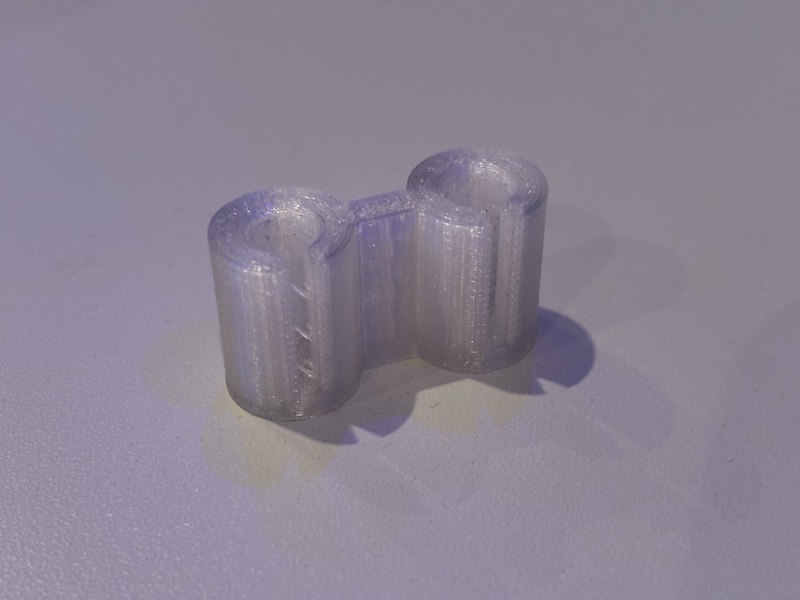
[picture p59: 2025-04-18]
mechanics/assembly/eb77-eh22_bauteil-14.JPG

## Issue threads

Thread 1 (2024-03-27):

Mutter an der Achse des Stiftarms löst sich beim Drucken mit der Zeit

justinotherguy, 2024-03-27:

justinotherguy, 2025-04-19:
fixed in https://github.com/section77/eggbot77/commit/1cb28c84671eb03e9e73089e0c43077b7dd873a7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
thx to @Bruder-Jo

Closed 2025-04-19.

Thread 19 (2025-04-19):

Arduino Board support package ESP32 ab Version 3.x funktioniert nicht

justinotherguy, 2025-04-19:
letzte kompatible Version ist 2.0.17
```
~/eggbot77/firmware/EggBot77/EBBHardware.cpp: In member function 'void EBBHardware::init()':
~/eggbot77/firmware/EggBot77/EBBHardware.cpp:53:5: error: 'ledcAttachPin' was not declared in this scope; did you mean 'ledcAttach'?
   53 |     ledcAttachPin(LED_BUILTIN, 1);
      |     ^~~~~~~~~~~~~
      |     ledcAttach
~/eggbot77/firmware/EggBot77/EBBHardware.cpp:54:5: error: 'ledcSetup' was not declared in this scope
   54 |     ledcSetup(LED_BUILTIN_LEDC_CH, 1200, 10);
      |     ^~~~~~~~~
exit status 1

Compilation error: 'ledcAttachPin' was not declared in this scope; did you mean 'ledcAttach'?
```

Andy1978, 2025-04-20:
https://github.com/espressif/arduino-esp32/blob/master/docs/en/migration_guides/2.x_to_3.0.rst#ledc

Andy1978, 2025-04-20:
See branch arduino-esp32_v2_to_v3 but I don't have hardware to test it

justinotherguy, 2025-04-20:
> See branch arduino-esp32_v2_to_v3 but I don't have hardware to test it

eggcellent! will give it a try and let you know

justinotherguy, 2025-04-22:
tested - results:
- steppers work fine
- servo does not respond - no error message visible, either

justinotherguy, 2025-04-22:
wrong pin, I guess

justinotherguy, 2025-04-22:
fixed with https://github.com/section77/eggbot77/commit/0128d29085827adc47fd672f1612245dcc59fdcd

Closed 2025-04-22.

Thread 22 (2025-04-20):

Python Issues in EggBot extension Funktion "Name Poem" in InkScape

c-ruttkies, 2025-04-20:
Ich habe Python issues mit einigen Funktionen in der InkScape extension:

Bei der Funktion "Extensions" -> "EggBot Contributed" -> "Name Poem"

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

wirft InkScape den Fehler:

```
Traceback (most recent call last):
  File "/home/christoph/.config/inkscape/extensions/eggbot_acrostic.py", line 267, in <module>
    e.run()
  File "/usr/share/inkscape/extensions/inkex/base.py", line 131, in run
    self.save_raw(self.effect())
  File "/home/christoph/.config/inkscape/extensions/eggbot_acrostic.py", line 236, in effect
    face1 = eval( 'hersheydata.' + name1 )
  File "<string>", line 1, in <module>
NameError: name 'hersheydata' is not defined
```

Ich schätze, dass das an dem auskommentierten import in eggbot_acrostic.py (Zeile 30) liegt:

`# import hersheydata            # data file w/ Hershey font data`

Der ist irgendwann mal rausgeflogen. Im originalen Repo (https://github.com/gesina/eggbot_extension/blob/master/extensions/eggbot_acrostic.py) ist die Zeile noch drin. Wenn man die einkommentiert, funktioniert es.

InkScape 1.1
Python 3.10.12

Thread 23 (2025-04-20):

Python Issues in EggBot extension Funktion "EggBot Control -> Plot" in InkScape

c-ruttkies, 2025-04-20:
Ich habe Python issues mit einigen Funktionen in der InkScape extension:

Bei der Funktion "Extensions" -> "EggBot Control" -> "Plot"

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

wirft InkScape den Fehler:

```
Traceback (most recent call last):
  File "/home/christoph/.config/inkscape/extensions/eggbot.py", line 1170, in <module>
    e.run()
  File "/usr/share/inkscape/extensions/inkex/base.py", line 131, in run
    self.save_raw(self.effect())
  File "/home/christoph/.config/inkscape/extensions/eggbot.py", line 199, in effect
    self.plotToEggBot()
  File "/home/christoph/.config/inkscape/extensions/eggbot.py", line 446, in plotToEggBot
    self.recursivelyTraverseSvg( self.svg, self.svgTransform )
  File "/home/christoph/.config/inkscape/extensions/eggbot.py", line 500, in recursivelyTraverseSvg
    matNew = ( Transform(matCurrent) @ Transform( node.get( "transform" ) ) ).matrix
TypeError: unsupported operand type(s) for @: 'Transform' and 'Transform'
```

Hängt das evtl mit meiner Python-Version zusammen?

InkScape 1.1
Python 3.10.12

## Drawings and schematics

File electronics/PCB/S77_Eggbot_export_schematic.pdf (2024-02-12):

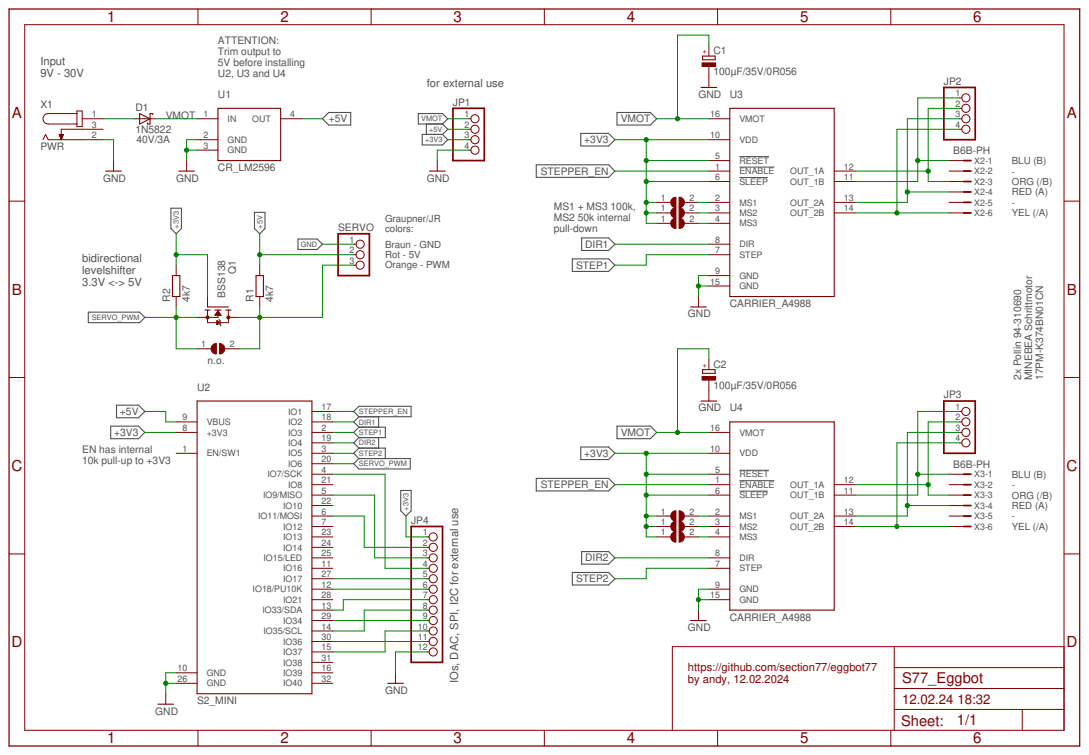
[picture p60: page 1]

PI, I2C for external use

29 | 9
14 | 10
30 | 11
15 | 12

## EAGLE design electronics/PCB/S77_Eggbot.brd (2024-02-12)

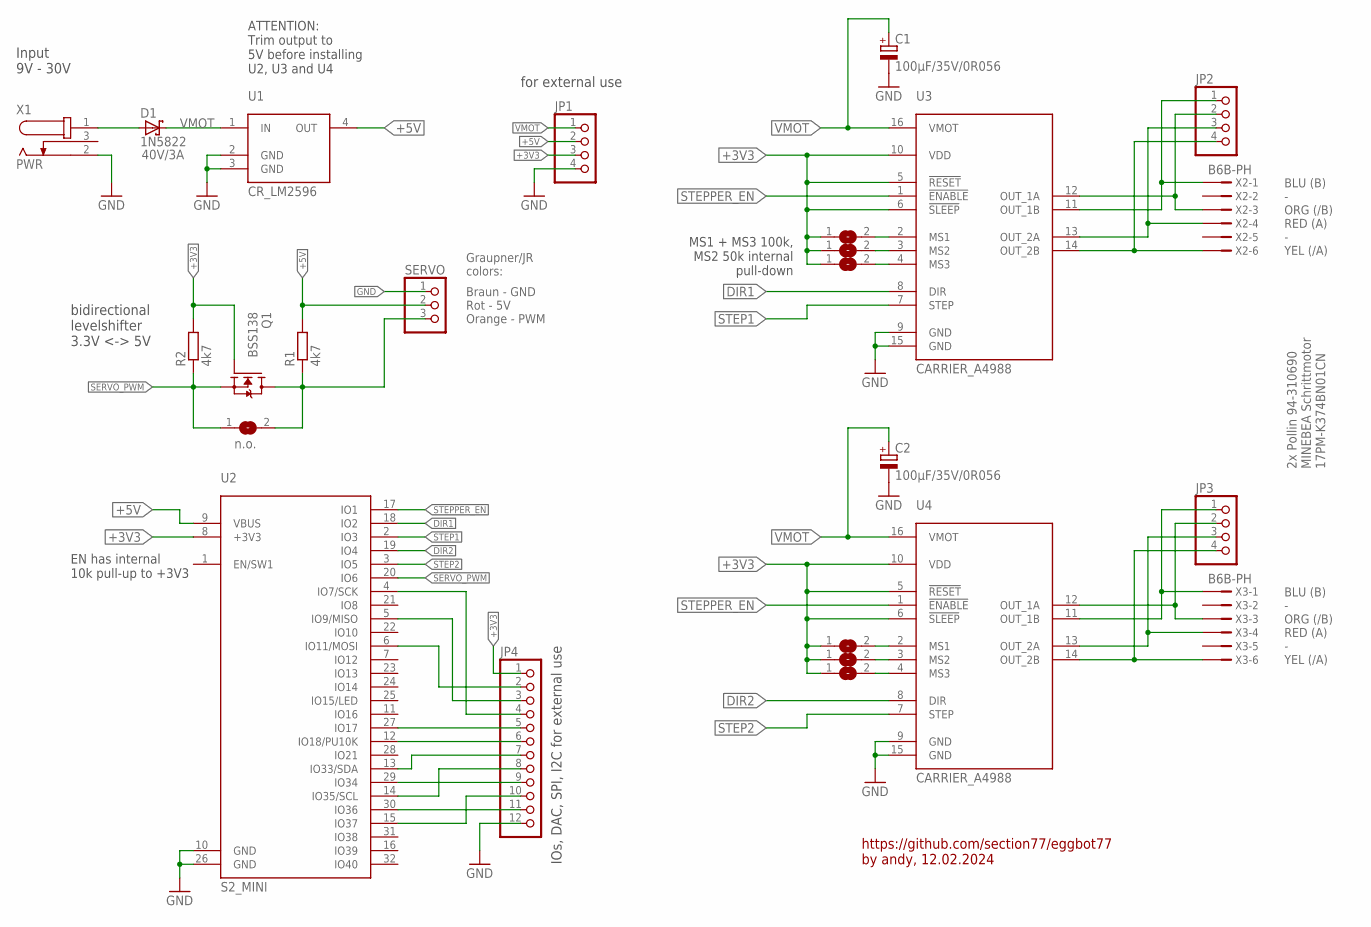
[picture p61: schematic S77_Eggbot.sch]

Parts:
C1, C2: 100µF/35V/0R056; E3,5-8; MPN EEUFR1V101
D1: 1N5822; DO201T15
JP1, JP2, JP3: PINHD-1X4; 1X04
JP4: PINHD-1X12; 1X12
Q1: BSS138; SOT23
R1, R2: 4k7; R1206
SERVO: PINHD-1X3; 1X03
SJ1, SJ2, SJ3, SJ4, SJ5, SJ6: SJ
SJ7: n.o.; SJ
U1: CR_LM2596
U2: S2_MINI
U3, U4: CARRIER_A4988
X1: PWR; POLLIN_JACK_A
X2, X3: B6B-PH

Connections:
+3V3: JP1.3, JP4.1, Q1.1 (G), R2.2, SJ1.1, SJ2.1, SJ3.1, SJ4.1, SJ5.1, SJ6.1, U2.8 (+3V3), U3.5 (!RESET), U3.6 (!SLEEP), U3.10 (VDD), U4.5 (!RESET), U4.6 (!SLEEP), U4.10 (VDD)
+5V: JP1.2, R1.2, SERVO.2, U1.4 (OUT), U2.9 (VBUS)
DIR1: U2.18 (IO2), U3.8 (DIR)
DIR2: U2.19 (IO4), U4.8 (DIR)
GND: C1.-, C2.-, JP1.4, JP4.12, SERVO.1, U1.2 (GND), U1.3 (GND), U2.10 (GND), U2.26 (GND), U3.9 (GND), U3.15 (GND), U4.9 (GND), U4.15 (GND), X1.2
unnamed: Q1.3 (D), R1.1, SERVO.3, SJ7.2
unnamed: JP2.1, U3.11 (OUT_1B), X2.1
unnamed: D1.A, X1.1
unnamed: JP2.2, U3.12 (OUT_1A), X2.3
unnamed: JP2.3, U3.13 (OUT_2A), X2.4
unnamed: JP2.4, U3.14 (OUT_2B), X2.6
unnamed: JP3.1, U4.11 (OUT_1B), X3.1
unnamed: JP3.2, U4.12 (OUT_1A), X3.3
unnamed: JP3.3, U4.13 (OUT_2A), X3.4
unnamed: JP3.4, U4.14 (OUT_2B), X3.6
unnamed: SJ1.2, U3.2 (MS1)
unnamed: SJ2.2, U3.3 (MS2)
unnamed: SJ3.2, U3.4 (MS3)
unnamed: SJ4.2, U4.2 (MS1)
unnamed: SJ5.2, U4.3 (MS2)
unnamed: SJ6.2, U4.4 (MS3)
unnamed: JP4.4, U2.4 (IO7/SCK)
unnamed: JP4.3, U2.5 (IO9/MISO)
unnamed: JP4.2, U2.6 (IO11/MOSI)
unnamed: JP4.5, U2.27 (IO17)
unnamed: JP4.6, U2.12 (IO18/PU10K)
unnamed: JP4.7, U2.13 (IO33/SDA)
unnamed: JP4.9, U2.29 (IO34)
unnamed: JP4.8, U2.14 (IO35/SCL)
unnamed: JP4.11, U2.30 (IO36)
unnamed: JP4.10, U2.15 (IO37)
SERVO_PWM: Q1.2 (S), R2.1, SJ7.1, U2.20 (IO6)
STEP1: U2.2 (IO3), U3.7 (STEP)
STEP2: U2.3 (IO5), U4.7 (STEP)
STEPPER_EN: U2.17 (IO1), U3.1 (!ENABLE), U4.1 (!ENABLE)
VMOT: C1.+, C2.+, D1.C, JP1.1, U1.1 (IN), U3.16 (VMOT), U4.16 (VMOT)

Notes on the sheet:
ATTENTION: Trim output to 5V before installing U2, U3 and U4
Input 9V - 30V
40V/3A
2x Pollin 94-310690 MINEBEA Schrittmotor 17PM-K374BN01CN
BLU (B) - ORG (/B) RED (A) - YEL (/A)
Braun - GND Rot - 5V Orange - PWM
MS1 + MS3 100k, MS2 50k internal pull-down
for external use
IOs, DAC, SPI, I2C for external use
EN has internal 10k pull-up to +3V3
https://github.com/section77/eggbot77 by andy, 12.02.2024
Graupner/JR colors:
bidirectional levelshifter 3.3V <-> 5V

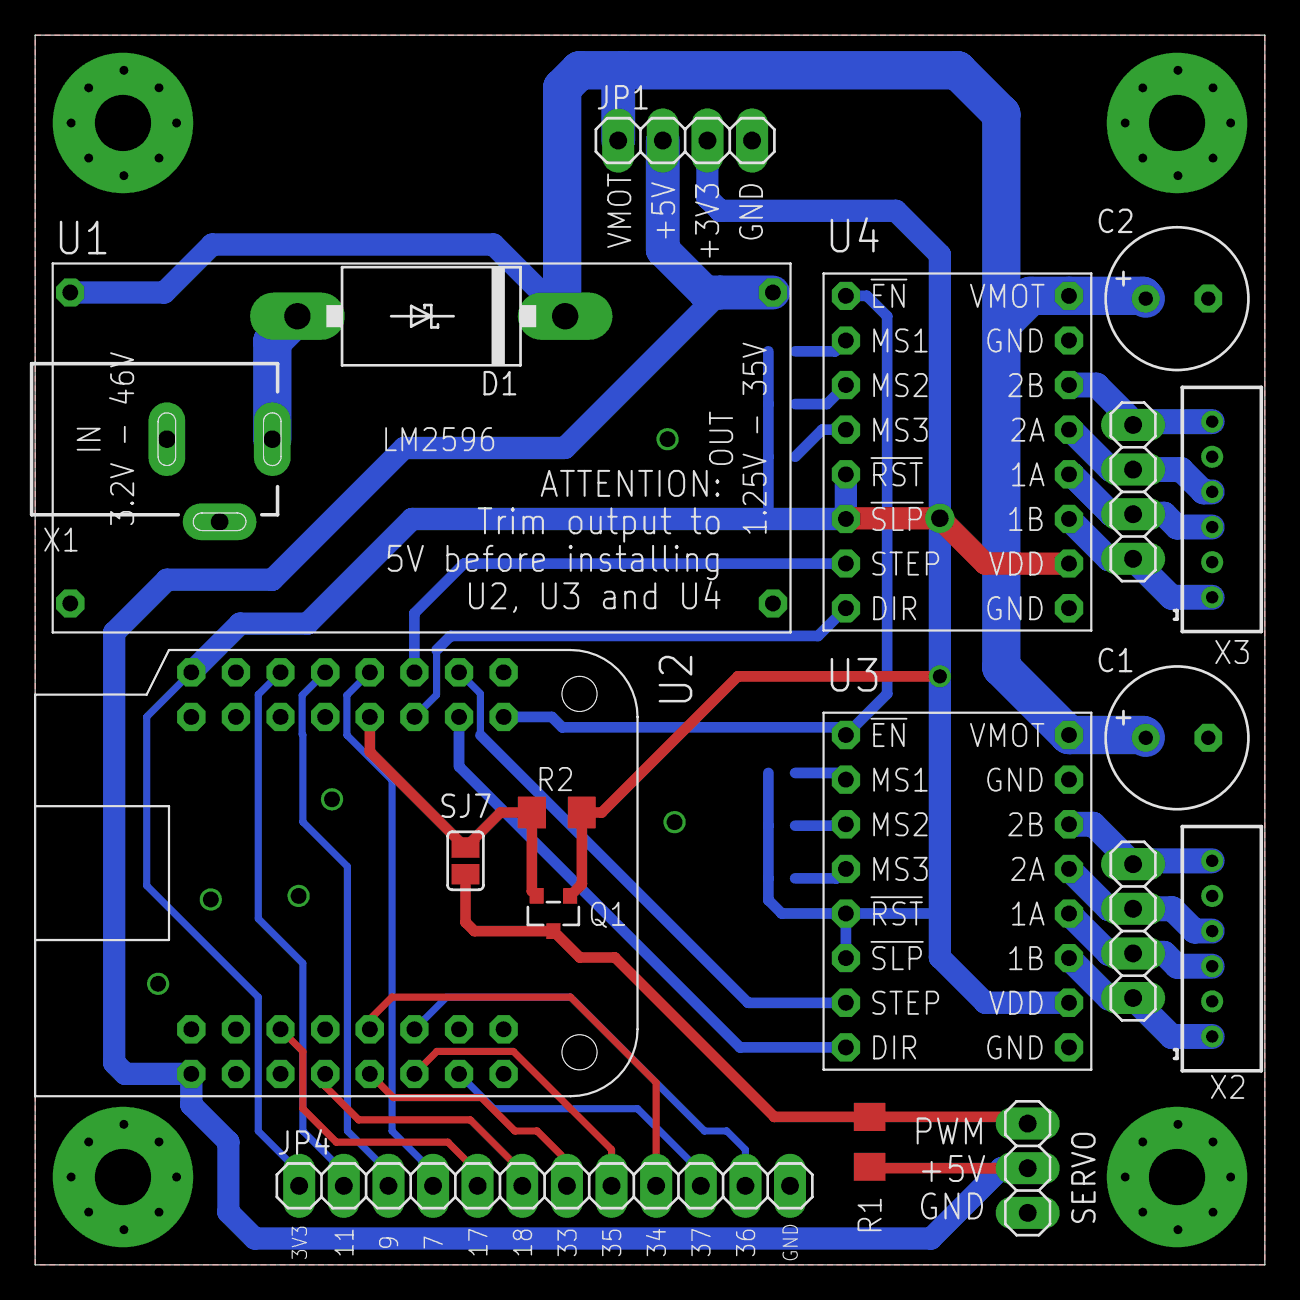
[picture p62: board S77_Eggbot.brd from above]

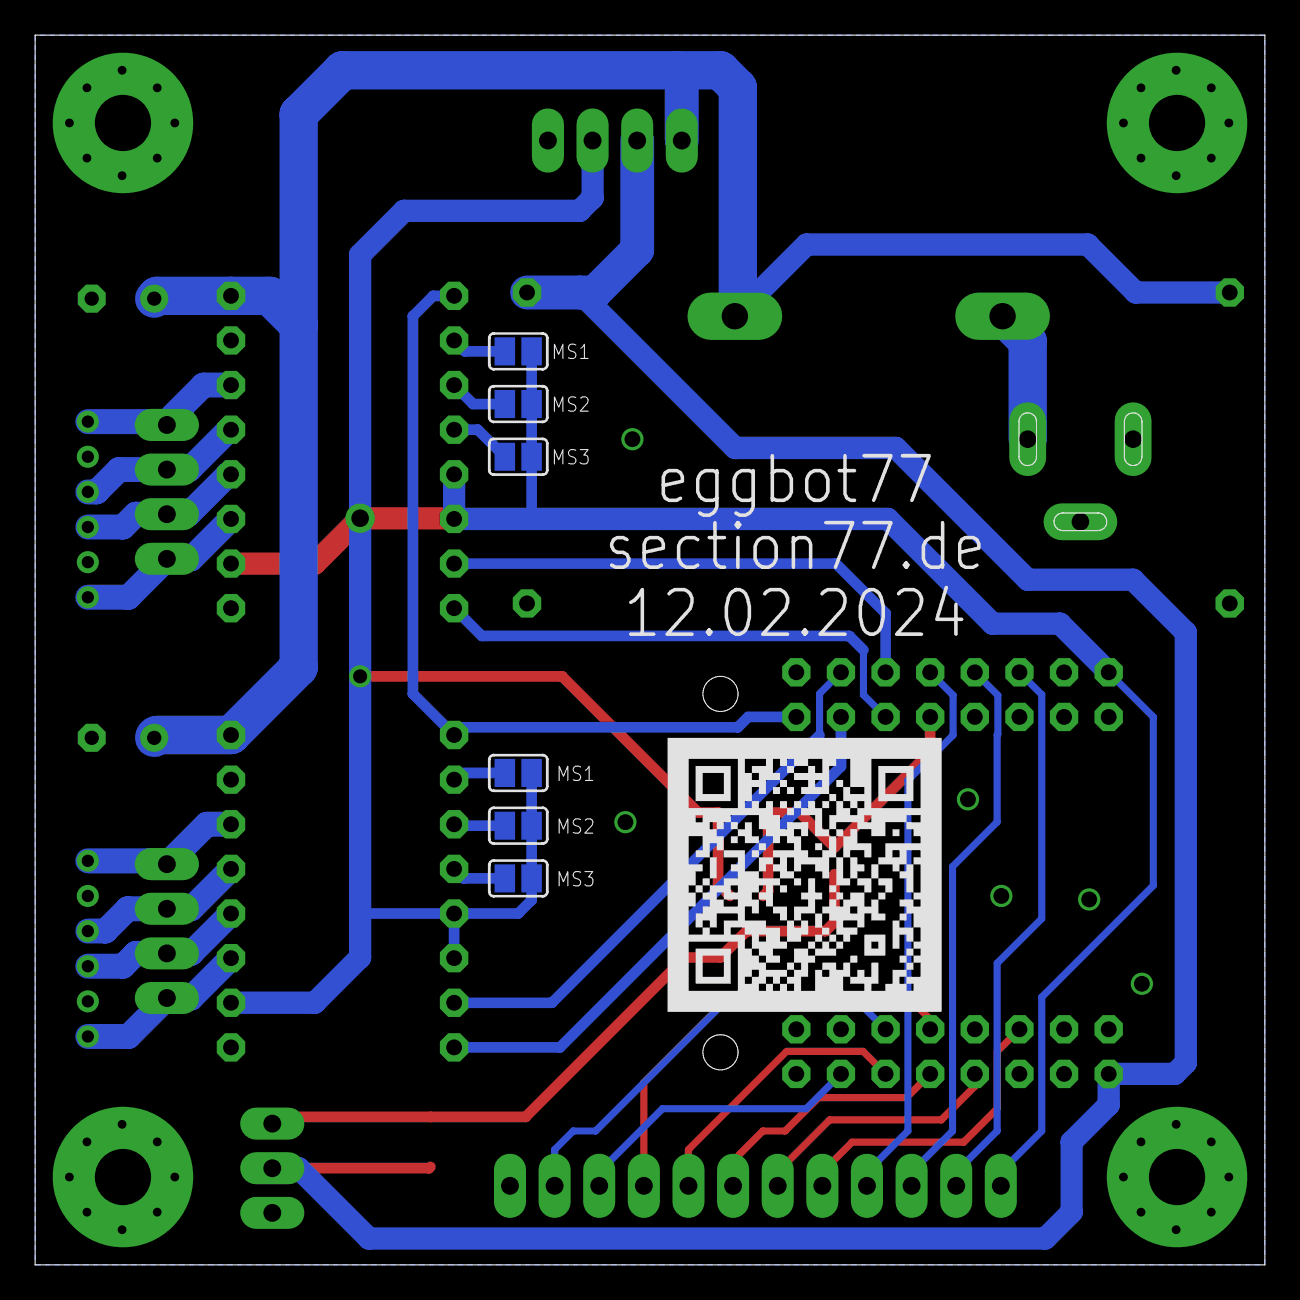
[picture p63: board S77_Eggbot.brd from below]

Board: 2 copper layers, 70.0 x 70.0 mm, 25 parts (6 on the bottom side), 36 nets.

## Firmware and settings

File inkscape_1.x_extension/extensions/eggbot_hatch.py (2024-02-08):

#!/usr/bin/env python

# eggbot_hatch.py
#
# Generate hatch fills for the closed paths (polygons) in the currently
# selected document elements.  If no elements are selected, then all the
# polygons throughout the document are hatched.  The fill rule is an odd/even
# rule: odd numbered intersections (1, 3, 5, etc.) are a hatch line entering
# a polygon while even numbered intersections (2, 4, 6, etc.) are the same
# hatch line exiting the polygon.
#
# This extension first decomposes the selected <path>, <rect>, <line>,
# <polyline>, <polygon>, <circle>, and <ellipse> elements into individual
# moveto and lineto coordinates using the same procedure that eggbot.py uses
# for plotting.  These coordinates are then used to build vertex lists.
# Only the vertex lists corresponding to polygons (closed paths) are
# kept.  Note that a single graphical element may be composed of several
# subpaths, each subpath potentially a polygon.
#
# Once the lists of all the vertices are built, potential hatch lines are
# "projected" through the bounding box containing all of the vertices.
# For each potential hatch line, all intersections with all the polygon
# edges are determined.  These intersections are stored as decimal fractions
# indicating where along the length of the hatch line the intersection
# occurs.  These values will always be in the range [0, 1].  A value of 0
# indicates that the intersection is at the start of the hatch line, a value
# of 0.5 midway, and a value of 1 at the end of the hatch line.
#
# For a given hatch line, all the fractional values are sorted and any
# duplicates removed.  Duplicates occur, for instance, when the hatch
# line passes through a polygon vertex and thus intersects two edges
# segments of the polygon: the end of one edge and the start of
# another.
#
# Once sorted and duplicates removed, an odd/even rule is applied to
# determine which segments of the potential hatch line are within
# polygons.  These segments found to be within polygons are then saved
# and become the hatch fill lines which will be drawn.
#
# With each saved hatch fill line, information about which SVG graphical
# element it is within is saved.  This way, the hatch fill lines can
# later be grouped with the element they are associated with.  This makes
# it possible to manipulate the two -- graphical element and hatch lines --
# as a single object within Inkscape.
#
# Note: we also save the transformation matrix for each graphical element.
# That way, when we group the hatch fills with the element they are
# filling, we can invert the transformation.  That is, in order to compute
# the hatch fills, we first have had apply ALL applicable transforms to
# all the graphical elements.  We need to do that so that we know where in
# the drawing  each of the graphical elements are relative to one another.
# However, this means that the hatch lines have been computed in a setting
# where no further transforms are needed.  If we then put these hatch lines
# into the same groups as the elements being hatched in the ORIGINAL
# drawing, then the hatch lines will have transforms applied again.  So,
# once we compute the hatch lines, we need to invert the transforms of
# the group they will be placed in and apply this inverse transform to the
# hatch lines.  Hence the need to save the transform matrix for every
# graphical element.

# Written by Daniel C. Newman for the Eggbot Project
# dan dot newman at mtbaldy dot us
# Last updated 28 November 2010
# 15 October 2010

# Updated by Windell H. Oskay, 6/14/2012
# Added tolerance parameter

# Update by Daniel C. Newman, 6/20/2012
# Add min span/gap width

# Updated by Windell H. Oskay, 1/8/2016
# Added live preview and correct issue with nonzero min gap 
# https://github.com/evil-mad/EggBot/issues/32

# Updated by Sheldon B. Michaels, 1/11/2016 thru 3/15/2016
# shel at shel dot net
# Added feature: Option to inset the hatch segments from boundaries
# Added feature: Option to join hatch segments that are "nearby", to minimize pen lifts
# The joins are made using cubic Bezier segments.
# https://github.com/evil-mad/EggBot/issues/36						

# Updated by Nathan Depew, 12/6/2017
# Modified hatch fill to create hatches as a relevant object it found on the SVG tree
# This prevents extremely complex plots from generating glitches
# Modifications are limited to recursivelyTraverseSvg and effect methods 
 
#
# Current software version:
# (v2.1.0, December 6, 2017)
# 
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
# You should have received a copy of the GNU General Public License
# along with this program; if not, write to the Free Software
# Foundation, Inc., 59 Temple Place, Suite 330, Boston, MA  02111-1307  USA

import inkex
from inkex.transforms import Transform

import inkex.bezier
import math
import plot_utils		# https://github.com/evil-mad/plotink

import lxml.etree


N_PAGE_WIDTH = 3200
N_PAGE_HEIGHT = 800

F_MINGAP_SMALL_VALUE = 0.0000000001		# Was 0.00001 in the original version which did not have joined lines.
										# Reducing this by a factor of 10^5 decreased probability of occurrence of
										# the bug in the original, which got confused when the path barely
										# grazed a corner.
BEZIER_OVERSHOOT_MULTIPLIER = 0.75		# evaluation of cubic Bezier curve equation value,
										# at x = 0, with
										# endpoints at ( -0.5, 0 ), ( +0.5, 0 )
										# and control points at ( -0.5, 1.0 ), ( +0.5, 1.0 )

RADIAN_TOLERANCE_FOR_COLINEAR = 0.1		# Pragmatically adjusted to allow adjacent segments from the same scan line, even short ones,
										# to be classified as having the same angle
RADIAN_TOLERANCE_FOR_ALTERNATING_DIRECTION = 0.1	# Pragmatic adjustment again, as with colinearity tolerance
RECURSION_LIMIT = 500					# Pragmatic - if too high, risk runtime python error; if too low, miss some chances for reducing pen lifts
EXTREME_POSITIVE_NUMBER = float( 1.0E70 )
EXTREME_NEGATIVE_NUMBER = float( -1.0E70 )
MIN_HATCH_LENGTH_AS_FRACTION_OF_HATCH_SPACING = 0.25		# set minimum hatch length to some function
															# (e.g. this multiplier) of the hatch spacing
'''
Geometry 101: Determining if two lines intersect

A line L is defined by two points in space P1 and P2.  Any point P on the
line L satisfies

	P = P1 + s (P2 - P1)

for some value of the real number s in the range (-infinity, infinity).
If we confine s to the range [0, 1] then we've described the line segment
with end points P1 and P2.

Consider now the line La defined by the points P1 and P2, and the line Lb
defined by the points P3 and P4.  Any points Pa and Pb on the lines La and
Lb therefore satisfy

	Pa = P1 + sa (P2 - P1)
	Pb = P3 + sb (P4 - P3)

for some values of the real numbers sa and sb.  To see if these two lines
La and Lb intersect, we wish to see if there are finite values sa and sb
for which

	Pa = Pb

Or, equivalently, we ask if there exists values of sa and sb for which
the equation

	P1 + sa (P2 - P1) = P3 + sb (P4 - P3)

holds.  If we confine ourselves to a two-dimensional plane, and take

	P1 = (x1, y1)
	P2 = (x2, y2)
	P3 = (x3, y3)
	P4 = (x4, y4)

we then find that we have two equations in two unknowns, sa and sb,

	x1 + sa ( x2 - x1 ) = x3 + sb ( x4 - x3 )
	y1 + sa ( y2 - y1 ) = y3 + sb ( y4 - y3 )

Solving these two equations for sa and sb yields,

	sa = [ ( y1 - y3 ) ( x4 - x3 ) - ( y4 - y3 ) ( x1 - x3 ) ] / d
	sb = [ ( y1 - y3 ) ( x2 - x1 ) - ( y2 - y1 ) ( x1 - x3 ) ] / d

where the denominator, d, is given by

	d = ( y4 - y3 ) ( x2 - x1 ) - ( y2 - y1 ) ( x4 - x3 )

Substituting these back for the point (x, y) of intersection gives

	x = x1 + sa ( x2 - x1 )
	y = y1 + sa ( y2 - y1 )

Note that

1. The lines are parallel when d = 0
2. The lines are coincident d = 0 and the numerators for sa & sb are zero
3. For line segments, sa and sb are in the range [0, 1]; any value outside
   that range indicates that the line segments do not intersect.
'''

def intersect( P1, P2, P3, P4 ):

	'''
	Determine if two line segments defined by the four points P1 & P2 and
	P3 & P4 intersect.  If they do intersect, then return the fractional
	point of intersection "sa" along the first line at which the
	intersection occurs.
	'''

	# Precompute these values -- note that we're basically shifting from
	#
	#		P = P1 + s (P2 - P1)
	#
	# to
	#
	# 		P = P1 + s D
	#
	# where D is a direction vector.  The solution remains the same of
	# course.  We'll just be computing D once for each line rather than
	# computing it a couple of times.

	D21x = P2[0] - P1[0]
	D21y = P2[1] - P1[1]
	D43x = P4[0] - P3[0]
	D43y = P4[1] - P3[1]

	# Denominator
	d = D21x * D43y - D21y * D43x

	# Return now if the denominator is zero
	if d == 0:
		return float( -1 )

	# For our purposes, the first line segment given
	# by P1 & P2 is the LONG hatch line running through
	# the entire drawing.  And, P3 & P4 describe the
	# usually much shorter line segment from a polygon.
	# As such, we compute sb first as it's more likely
	# to indicate "no intersection".  That is, sa is
	# more likely to indicate an intersection with a
	# much a long line containing P3 & P4.

	nb = ( P1[1] - P3[1] ) * D21x - ( P1[0] - P3[0] ) * D21y

	# Could first check if abs(nb) > abs(d) or if
	# the signs differ.
	sb = float( nb ) / float( d )
	if ( sb < 0 ) or ( sb > 1 ):
		return float( -1 )

	na = ( P1[1] - P3[1] ) * D43x -  ( P1[0] - P3[0] ) * D43y
	sa = float( na ) / float( d )
	if ( sa < 0 ) or ( sa > 1 ):
		return float( -1 )

	return sa

def interstices( self, P1, P2, paths, hatches, bHoldBackHatches, fHoldBackSteps ):

	'''
	For the line L defined by the points P1 & P2, determine the segments
	of L which lie within the polygons described by the paths stored in
	"paths"

	P1 -- (x,y) coordinate [list]
	P2 -- (x,y) coordinate [list]
	paths -- Dictionary of all the paths to check for intersections

	When an intersection of the line L is found with a polygon edge, then
	the fractional distance along the line L is saved along with the
	lxml.etree node which contained the intersecting polygon edge.  This
	fractional distance is always in the range [0, 1].

	Once all polygons have been checked, the list of fractional distances
	corresponding to intersections is sorted and any duplicates removed.
	It is then assumed that the first intersection is the line L entering
	a polygon; the second intersection the line leaving the polygon.  This
	line segment defined by the first and second intersection points is
	thus a hatch fill line we sought to generate.  In general, our hatch
	fills become the line segments described by intersection i and i+1
	with i an odd value (1, 3, 5, ...).  Since we know the lxml.etree node
	corresponding to each intersection, we can then correlate the hatch
	fill lines to the graphical elements in the original SVG document.
	This enables us to group hatch lines with the elements being hatched.

	The hatch line segments are returned by populating a dictionary.
	The dictionary is keyed off of the lxml.etree node pointer.  Each
	dictionary value is a list of 4-tuples,

		(x1, y1, x2, y2)

	where (x1, y1) and (x2, y2) are the (x,y) coordinates of the line
	segment's starting and ending points.
	'''

	dAndA = []
	# P1 & P2 is the hatch line
	# P3 & P4 is the polygon edge to check
	for path in paths:
		for subpath in paths[path]:
			P3 = subpath[0]
			for P4 in subpath[1:]:
				s = intersect( P1, P2, P3, P4 )
				if ( s >= 0.0 ) and ( s <= 1.0 ):
					# Save this intersection point along the hatch line
					if bHoldBackHatches:
						# We will need to know how the hatch meets the polygon segment, so that we can
						# calculate the end of a shorter line that stops short
						# of the polygon segment.
						# We compute the angle now while we have the information required,
						# but do _not_ apply it now, as we need the real,original, intersects
						# for the odd/even inside/outside operations yet to come.
						# Note that though the intersect() routine _could_ compute the join angle,
						# we do it here because we go thru here much less often than we go thru intersect().
						angleHatchRadians = math.atan2( -( P2[1] - P1[1] ) ,( P2[0] - P1[0] ) )			# from P1 toward P2, cartesian coordinates
						angleSegmentRadians = math.atan2( -( P4[1] - P3[1] ) ,( P4[0] - P3[0] ) )		# from P3 toward P4, cartesian coordinates
						angleDifferenceRadians = angleHatchRadians - angleSegmentRadians
						# coerce to range -pi to +pi
						if ( angleDifferenceRadians > math.pi ):
							angleDifferenceRadians -= 2 * math.pi
						elif (angleDifferenceRadians < -math.pi ):
							angleDifferenceRadians += 2 * math.pi
						fSinOfJoinAngle = math.sin( angleDifferenceRadians )
						fAbsSinOfJoinAngle = abs( fSinOfJoinAngle )
						fPreliminaryLengthToBeRemovedFromPt = 0
						if (fAbsSinOfJoinAngle != 0.0):								# Worrying about case of intersecting a segment parallel to the hatch
							fPreliminaryLengthToBeRemovedFromPt = fHoldBackSteps / fAbsSinOfJoinAngle
							bUnconditionallyExciseHatch = False
						else:	# if (fSinOfJoinAngle != 0.0):
							bUnconditionallyExciseHatch = True
						# if (fAbsSinOfJoinAngle != 0.0): else:
						
						if ( not bUnconditionallyExciseHatch):
							# if ( fPreliminaryLengthToBeRemovedFromPt > ( distance from intersection to relevant end + fHoldbackSteps ) ):
							#	  fFinalLengthToBeRemovedFromPt = ( distance from intersection to relevant end + fHoldbackSteps )
							# The relevant end of the segment is the end from which the hatch approaches at an acute angle.
							I = [0,0]
							I[0] = P1[0] + s * ( P2[0] - P1[0] )		# compute intersection point of hatch with segment
							I[1] = P1[1] + s * ( P2[1] - P1[1] )		# intersecting hatch line starts at P1, vectored toward P2,
																		#	but terminates at intersection I
							# Note that atan2 returns answer in range -pi to pi
							# Which end is the approach end of the hatch to the segment?
							# The dot product tells the answer:
							#	if dot product is positive, P2 is at the P4 end,
							#	else P2 is at the P3 end
							# We really don't need to take the time to actually take
							# 	the cosine of the angle, we are just interested in
							#	the quadrant within which the angle lies.
							# I'm sure there is an elegant way to do this, but I'll settle for results just now.
							# If the angle is in quadrants I or IV then P4 is the relevant end, otherwise P3 is
							# nb: Y increases down, rather than up
							# nb: difference angle has been forced to the range -pi to +pi
							if ( abs(angleDifferenceRadians) < math.pi / 2 ):
								# It's near the P3 the relevant end from which the hatch departs
								fDistanceFromIntersectionToRelevantEnd = math.hypot( P3[0] - I[0], P3[1] - I[1] )
								fDistanceFromIntersectionToIrrelevantEnd = math.hypot( P4[0] - I[0], P4[1] - I[1] )
							else:	# if ( abs(angleDifferenceRadians) < math.pi / 2 )
								# It's near the P4 end from which the hatch departs
								fDistanceFromIntersectionToRelevantEnd = math.hypot( P4[0] - I[0], P4[1] - I[1] )
								fDistanceFromIntersectionToIrrelevantEnd = math.hypot( P3[0] - I[0], P3[1] - I[1] )
							# if ( abs(angleDifferenceRadians) < math.pi / 2 ): else:

							# Now, the problem defined in issue 22 is that we may not need to remove the
							# entire preliminary length we've calculated.  This problem occurs because
							# we have so far been considering the polygon segment as a line of infinite extent.
							# Thus, we may be holding back at a point where no holdback is required, when
							# calculated holdback is well beyond the position of the segment end.
							
							# To make matters worse, we do not currently know whether we're
							# starting a hatch or terminating a hatch, because the duplicates have
							# yet to be removed.  All we can do then, is calculate the required
							# line shortening for both possibilities - and then choose the correct
							# one after duplicate-removal, when actually finalizing the hatches.
							
							# Let's see if either end, or perhaps both ends, has a case of excessive holdback
							
							# First, default assumption is that neither end has excessive holdback
							fFinalLengthToBeRemovedFromPtWhenStartingHatch = fPreliminaryLengthToBeRemovedFromPt
							fFinalLengthToBeRemovedFromPtWhenEndingHatch = fPreliminaryLengthToBeRemovedFromPt
							
							# Now check each of the two ends
							if ( fPreliminaryLengthToBeRemovedFromPt > ( fDistanceFromIntersectionToRelevantEnd + fHoldBackSteps ) ):
								# Yes, would be excessive holdback approaching from this direction
								fFinalLengthToBeRemovedFromPtWhenStartingHatch = fDistanceFromIntersectionToRelevantEnd + fHoldBackSteps
							# if ( fPreliminaryLengthToBeRemovedFromPt > ( fDistanceFromIntersectionToRelevantEnd + fHoldBackSteps ) ):
							if ( fPreliminaryLengthToBeRemovedFromPt > ( fDistanceFromIntersectionToIrrelevantEnd + fHoldBackSteps ) ):
								# Yes, would be excessive holdback approaching from other direction
								fFinalLengthToBeRemovedFromPtWhenEndingHatch = fDistanceFromIntersectionToIrrelevantEnd + fHoldBackSteps
							# if ( fPreliminaryLengthToBeRemovedFromPt > ( fDistanceFromIntersectionToIrrelevantEnd + fHoldBackSteps ) ):

							dAndA.append( ( s, path, fFinalLengthToBeRemovedFromPtWhenStartingHatch, fFinalLengthToBeRemovedFromPtWhenEndingHatch ) )
						else:	# if ( not bUnconditionallyExciseHatch):
							dAndA.append( ( s, path, 123456.0, 123456.0 ) )			# Mark for complete hatch excision, hatch is parallel to segment
																			# Just a random number guaranteed large enough to be longer than any hatch length
						# if ( not bUnconditionallyExciseHatch): else :
					else:	# if bHoldBackHatches:
						dAndA.append( ( s, path, 0, 0 ) )			# zero length to be removed from hatch
					# if bHoldBackHatches: else:
				# if ( s >= 0.0 ) and ( s <= 1.0 ):	
				P3 = P4
			# for P4 in subpath[1:]:
		# for subpath in paths[path]:
	# for path in paths:

	# Return now if there were no intersections
	if len( dAndA ) == 0:
		return None

	dAndA.sort()
	
	# Remove duplicate intersections.  A common case where these arise
	# is when the hatch line passes through a vertex where one line segment
	# ends and the next one begins.

	# Having sorted the data, it's trivial to just scan through
	# removing duplicates as we go and then truncating the array
	
	n = len( dAndA )
	ilast = i = 1
	last = dAndA[0]
	while i < n:
		if ( ( abs( dAndA[i][0] - last[0] ) ) > F_MINGAP_SMALL_VALUE ):
			dAndA[ilast] = last = dAndA[i]
			ilast += 1
		i += 1
	dAndA = dAndA[:ilast]
	if len( dAndA ) < 2:
		return

	# Now, entries with even valued indices into sa[] are where we start
	# a hatch line and odd valued indices where we end the hatch line.

	last_dAndA = None
	i = 0
	while i < ( len( dAndA ) - 1 ):
	#for i in range( 0, len( sa ) - 1, 2 ):
		if dAndA[i][1] not in hatches:
			hatches[dAndA[i][1]] = []
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

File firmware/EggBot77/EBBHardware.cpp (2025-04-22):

#include "EBBHardware.h"
#include "config.h"

#include <EEPROM.h>

#define EEPROM_PEN_UP_POS 0
#define EEPROM_PEN_DOWN_POS 2

// https://rn-wissen.de/wiki/index.php/Servos
// width in µs
#define SERVO_MIN_PULSE_WIDTH 950
#define SERVO_MAX_PULSE_WIDTH 2050
#define SERVO_DEFAULT_PULSE_WIDTH 1500

EBBHardware::EBBHardware(Stream& stream)
    : EBBParser(stream)
    , mRotMotor(X_STEP_PIN, X_DIR_PIN)
    , mPenMotor(Y_STEP_PIN, Y_DIR_PIN)
    , mPenState(false)
    , mPenUpPos(SERVO_DEFAULT_PULSE_WIDTH - 200) // can be overwritten from EBB-Command SC
    , mPenDownPos(SERVO_DEFAULT_PULSE_WIDTH) // can be overwritten from EBB-Command SC
    , mMotorEnabled(false)
    , mPrgButtonState(false)
#ifdef PRG_BUTTON_PIN
    , mPrgButtonToggle(PRG_BUTTON_PIN)
#endif
#ifdef PEN_TOGGLE_BUTTON_PIN
    , mPenToggle(PEN_TOGGLE_BUTTON_PIN)
#endif
#ifdef MOTORS_BUTTON_PIN
    , mMotorsToggle(MOTORS_BUTTON_PIN)
#endif
{
}

void EBBHardware::init()
{
    EEPROM.get(EEPROM_PEN_UP_POS, mPenUpPos);
    EEPROM.get(EEPROM_PEN_DOWN_POS, mPenDownPos);

    pinMode(X_ENABLE_PIN, OUTPUT);
    pinMode(Y_ENABLE_PIN, OUTPUT);
#ifdef ENGRAVER_PIN
    pinMode(ENGRAVER_PIN, OUTPUT);
#endif
    //mPenServo.attach(SERVO_PIN);

    enableMotor(0, false);
    enableMotor(1, false);
    setPenState(mPenState, 0);

    // attach onboard LED to channel 1
    // arduino-esp32 version 2.x
    //ledcAttachPin(LED_BUILTIN, LED_BUILTIN_LEDC_CH);
    //ledcSetup(LED_BUILTIN_LEDC_CH, 1200, 10);

    // arduino-esp32 version 3.x
    ledcAttach(LED_BUILTIN, 1200, 10);


    // attach Servo PWM pin to channel 2
    // arduino-esp32 version 2.x
    //ledcAttachPin(SERVO_PIN, SERVO_PIN_LEDC_CH);
    //ledcSetup(SERVO_PIN_LEDC_CH, 50, 10);

    // arduino-esp32 version 3.x
    ledcAttach(SERVO_PIN, 50, 10);
}

void EBBHardware::processEvents()
{
#ifdef PRG_BUTTON_PIN
    if (mPrgButtonToggle.wasPressed()) {
        mPrgButtonState = true;
    }
#endif

#ifdef PEN_TOGGLE_BUTTON_PIN
    if (mPenToggle.wasPressed()) {
        setPenState(!getPenState(), 0);
    }
#endif

#ifdef MOTORS_BUTTON_PIN
    if (mMotorsToggle.wasPressed()) {
        if (mMotorEnabled) {
            enableMotor(0, false);
            enableMotor(1, false);
        } else {
            enableMotor(0, true);
            enableMotor(1, true);
        }
    }
#endif
    parseStream();

    mPenMotor.update();
    mRotMotor.update();
}

void EBBHardware::enableMotor(int axis, bool state)
{
    const uint8_t pin = (axis == 0) ? X_ENABLE_PIN : Y_ENABLE_PIN;

    digitalWrite(pin, state ? LOW : HIGH);

    mMotorEnabled = state;
}

void EBBHardware::stepperMove(int duration, int numPenSteps, int numRotSteps)
{
    moveToDestination();

    // Genuine EggBots are almost all using 16 microstepping.
    // A standard nema 17 stepper has 200 steps.
    // With 16 microstepping 200 * 16 = 3200 steps for a full revolution.
    // If your EggDuino does not have the same number of steps,
    // you need to adjust the inkscape plugin STEP_SCALE variable inside eggbot_conf.py.

    // set Coordinates and Speed
    if (numRotSteps == 0 && numPenSteps == 0) {
        delay(duration);
    } else {
        mRotMotor.setTarget(numRotSteps, duration);
        mPenMotor.setTarget(numPenSteps, duration);
    }
}

void EBBHardware::moveToDestination()
{
    while (mPenMotor.remainingSteps() || mRotMotor.remainingSteps()) {
        mPenMotor.update(); // Moving.... moving... moving....
        mRotMotor.update();
    }
}

void EBBHardware::setPinOutput(char port, int pin, int value)
{
    // PO,B,3,0 = disable engraver
    // PO,B,3,1 = enable engraver
#ifdef ENGRAVER_PIN
    if (port == 'B' && pin == 3) {
        digitalWrite(ENGRAVER_PIN, value);
    }
#endif
}

void EBBHardware::setEngraverState(bool state, int power)
{
#ifdef ENGRAVER_PIN
    digitalWrite(ENGRAVER_PIN, state);
#endif
}

void EBBHardware::setPenState(bool up, short delayMs)
{
    moveToDestination();
    uint16_t pwm_val = ((up)? mPenUpPos:mPenDownPos) / 20000.0f * 1024;
    ledcWrite(SERVO_PIN_LEDC_CH, pwm_val);
    mPenState = up;
    delay(delayMs);
}

bool EBBHardware::getPenState()
{
    return mPenState;
}

void EBBHardware::setPenUpPos(int percent)
{
    // transformation from percent to PWM-Servo
    mPenUpPos = SERVO_MIN_PULSE_WIDTH + (SERVO_MAX_PULSE_WIDTH - SERVO_MIN_PULSE_WIDTH) * percent / 100.f;
    EEPROM.put(EEPROM_PEN_UP_POS, mPenUpPos);
}

void EBBHardware::setPenDownPos(int percent)
{
    // transformation from percent to PWM-Servo
    mPenDownPos = SERVO_MIN_PULSE_WIDTH + (SERVO_MAX_PULSE_WIDTH - SERVO_MIN_PULSE_WIDTH) * percent / 100.f;
    EEPROM.put(EEPROM_PEN_DOWN_POS, mPenDownPos);
}

bool EBBHardware::getPrgButtonState()
{
    bool state = mPrgButtonState;
    mPrgButtonState = false;
    return state;
}

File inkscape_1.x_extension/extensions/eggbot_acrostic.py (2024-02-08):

# eggbot_acrostic.py
#
# Render an acrostic poem using the Hershey fonts
#
# This extension requires the hersheydata.py file which is part of the
# Hershey Text rendering extension written by Windell H. Oskay of
# www.evilmadscientist.com.  Information on that extension may be found at
#
#   http://www.evilmadscientist.com/go/hershey
#
# Copyright 2011, Daniel C. Newman,
#
# Significant portions of this code were written by Windell H. Oskay and are
# Copyright 2011, Windell H. Oskay, www.evilmadscientist.com
#
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
#import hersheydata			# data file w/ Hershey font data
import inkex
import lxml.etree

WIDTH     = 3200
HEIGHT    = 800
MAX_H     = 32		# Maximum height of a Hershey font character (parens)
LINE_SKIP = 6		# Baseline skip between lines of text

# Mapping table to map the names used here to the corresponding
# names used in hersheydata.py.  This helps prevent end users from
# being impacted by a name change in hersheydata.py.  This can also
# be used to deal with a face being removed from hersheydata.py

map_our_names_to_hersheydata = {
	'astrology' : 'astrology',
	'cursive' : 'cursive',
	'cyrillic' : 'cyrillic',
	'futural' : 'futural',
	'futuram' : 'futuram',
	'gothiceng' : 'gothiceng',
	'gothicger' : 'gothicger',
	'gothicita' : 'gothicita',
	'greek' : 'greek',
	'japanese' : 'japanese',
	'markers' : 'markers',
	'mathlow' : 'mathlow',
	'mathupp' : 'mathupp',
	'meteorology' : 'meteorology',
	'music' : 'music',
	'scriptc' : 'scriptc',
	'scripts' : 'scripts',
	'symbolic' : 'symbolic',
	'timesg' : 'timesg',
	'timesi' : 'timesi',
	'timesib' : 'timesib',
	'timesr' : 'timesr',
	'timesrb' : 'timesrb' }

# The following two routines are lifted with impunity from Windell H. Oskay's
# hershey.py Hershey Text extension for Inkscape.  They are,
# Copyright 2011, Windell H. Oskay, www.evilmadscientist.com

def draw_svg_text(char, face, offset, vertoffset, parent):

	style = { 'stroke': '#000000', 'fill': 'none' }
	pathString = face[char]
	splitString = pathString.split()
	midpoint = offset - int(splitString[0])
	i = pathString.find("M")
	if i >= 0:
		pathString = pathString[i:] #portion after first move
		trans = 'translate(' + str(midpoint) + ',' + str(vertoffset) + ')'
		text_attribs = {'style':str(inkex.Style(style)), 'd':pathString, 'transform':trans}
		lxml.etree.SubElement(parent, inkex.addNS('path','svg'), text_attribs)
	return midpoint + int(splitString[1]) 	#new offset value

def renderText( parent, w, y, text, typeface ):

	'''
	Render a string of text starting from the point (w, y) and using
	the supplied typeface data.
	'''

	if ( text is None ) or ( text == '' ):
		return

	spacing = 3  # spacing between letters
	letterVals = [ ord( q ) - 32 for q in text ]

	for q in letterVals:
		if ( q < 0 ) or ( q > 95 ):
			w += 2 * spacing
		else:
			w = draw_svg_text( q, typeface, w, y, parent )

	return w

def renderLine( parent, x, y, line, typeface1, typeface2 ):

	'''
	Render a single line of text:
	+ The text runs horizontally from left to right starting at the point (x,y)
	+ The first character of the line is written using "typeface1"
	+ The remainder of the line of text is written using "typeface2"

	The entire line is stored as individual paths which are child elements
	of the SVG element "parent".  The text in typeface2 (line[1:]) is also
	placed in it's own subgroup.  The leading character is not placed in
	that subgroup.  The reasoning is that the user may want to pick out
	the first character of each line of text and put them in another layer
	for plotting in a different color.
	'''

	# Return now if there's nothing to do
	if ( line is None ) or ( line == '' ):
		return

	# Render the first character
	x = renderText( parent, x, y, [ line[0] ], typeface1 )

	# Render the rest of the line
	line = line[1:]
	if line == '':
		return
	g = lxml.etree.SubElement( parent, 'g' )
	renderText( g, x, y, line, typeface2 )

class AcrosticText( inkex.Effect ):

	def __init__( self ):

		inkex.Effect.__init__( self )
		self.arg_parser.add_argument( "--tab",	#NOTE: value is not used.
			type=str, dest="tab", default="splash",
			help="The active tab when Apply was pressed" )
		self.arg_parser.add_argument( "--line01",
			type=str, dest="line1", default="")
		self.arg_parser.add_argument( "--line02",
			type=str, dest="line2", default="")
		self.arg_parser.add_argument( "--line03",
			type=str, dest="line3", default="")
		self.arg_parser.add_argument( "--line04",
			type=str, dest="line4", default="")
		self.arg_parser.add_argument( "--line05",
			type=str, dest="line5", default="")
		self.arg_parser.add_argument( "--line06",
			type=str, dest="line6", default="")
		self.arg_parser.add_argument( "--line07",
			type=str, dest="line7", default="")
		self.arg_parser.add_argument( "--line08",
			type=str, dest="line8", default="")
		self.arg_parser.add_argument( "--line09",
			type=str, dest="line9", default="")
		self.arg_parser.add_argument( "--line10",
			type=str, dest="line10", default="")
		self.arg_parser.add_argument( "--line11",
			type=str, dest="line11", default="")
		self.arg_parser.add_argument( "--line12",
			type=str, dest="line12", default="")
		self.arg_parser.add_argument( "--face1",
			type=str, dest="face1", default="scriptc",
			help="Leading font typeface" )
		self.arg_parser.add_argument( "--face2",
			type=str, dest="face2", default="scripts",
			help="Secondary typeface" )
		self.arg_parser.add_argument( "--flip", type=inkex.Boolean,
			dest="flip", default=False,
			help="Flip the text for plotting with the egg's bottom at the egg motor" )
		self.arg_parser.add_argument( "--stretch",
			type=inkex.Boolean, dest="stretch", default=True,
			help="Stretch the text horizontally to account for egg distortions" )

	def effect( self ):

		# Process the lines, ignoring leading or trailing blank lines
		# and collapsing multiple internal runs of blank lines into a
		# single blank line.
		lines = []
		prior_empty = False
		for i in range( 1, 13 ):
			line = eval( 'self.options.line' + str( i ) ).strip()
			if line == '':
				if len( lines ) != 0:
					prior_empty = True
			else:
				if prior_empty:
					lines.append( '' )
					prior_empty = False
				lines.append( line )

		# Return now if there are no lines to print
		line_count = len( lines )
		if line_count == 0:
			return

		# Determine how much vertical room we need for our text
		h = line_count * MAX_H + ( line_count - 1 ) * LINE_SKIP

		svg = self.document.getroot()
		doc_height = self.svg.unittouu( svg.attrib['height'] )
		if doc_height <= 0:
			doc_height = HEIGHT
		doc_width = self.svg.unittouu( svg.attrib['width'] )
		if doc_width <= 0:
			doc_width = WIDTH

		# Scale to doc_height pixels high
		scale_y = float( doc_height ) / float( h )
		if self.options.stretch:
			scale_x = scale_y * 1.5
		else:
			scale_x = scale_y
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

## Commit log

2024-01-17 Add Eagle schematic and library
    [S77_Eggbot.brd, S77_Eggbot.sch]
2024-01-20 add most stl files
    [Box_Intersecting_Rods.stl, Faucet.stl, Pen_Stepper_Holder-V2.stl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]
2024-01-21 add remaining print files and update readme
    [Rotational_Stepper_Holder.stl, penarm-stronger.scad, spring-3mm.scad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]
2024-01-24 WIP: fix board dimension and place components
    [S77_Eggbot.brd, S77_Eggbot.sch]
2024-01-24 first version of schematic and layout
    [S77_Eggbot.brd, S77_Eggbot.sch]
2024-01-25 PCB: fix smaller details, update docs
    [S77_Eggbot.brd, S77_Eggbot.sch]
2024-01-25 Add QR Code to board layout, export gerber files
    [S77_Eggbot.brd]
2024-01-25 Add section77.de to board, increase clearance to 8mil
    [S77_Eggbot.brd]
2024-02-05 increase diameter for spring bolt
    [toolmount.scad, toolmount.stl]
2024-02-05 Fix: swap Pin 1 and 2 on barrel jack X1
    [S77_Eggbot.brd, S77_Eggbot.sch]
2024-02-09 Move firmware in separate directory, arduino-ide complains if not
2024-02-09 docs: Add esp32_technical_reference_manual_en
2024-02-09 PCB: update date
    [S77_Eggbot.brd, S77_Eggbot.sch]
2024-02-09 firmware: Use ESP32 LED Controller PWM for pen servo up/down
2024-02-09 firmware doc: Image of board select in arduino IDE
2024-02-09 inkscape extension, add new PID and name after update to arduino IDE 2.3.0
2024-02-09 playground: simple script to test steppers
2024-02-10 Firmware: fix minimal STEP width (1µs for A4988) on ESP32 S2 mini
    [Stepper.cpp]
2024-02-12 Fix footprint for pollin 5.5/2.1mm and 5.5/2.5mm jacks
    [S77_Eggbot.brd, S77_Eggbot.sch]
2024-02-12 EBBHardware.cpp: use define for Servo Pin LED Controller channel
2024-02-12 PCB: added 3.3V<->5V levelshifter for servo PWM, update exports
    [S77_Eggbot.brd, S77_Eggbot.sch]
2024-02-15 modify spring to suit new screw type
    [spring-3mm.scad, spring-3mm.stl]
2024-02-15 remove old variants of stl files
    [Pen_Stepper_Holder-V2.stl, Rotational_Stepper_Holder.stl]
2024-02-15 add new version of stepper holder, created by michaelf, precision adjustments by bruder-jo - thank you! :)
    [stepperholder_Pen_6mm.stl]
2024-02-15 add rotational stepper holder with holes drilled all the way - thx to bruder-jo!
    [Rotational_Stepper_Holder_gelocht.stl]
2024-02-16 firmware/EggBot77: fix conditional compiling without engraver
    [EBBHardware.cpp, config.h]
2024-02-22 extend hardware test to drive both steppers and pen servo
2024-03-15 BOM.md: Reichelt Bauteile für 5V PWM hinzugefügt
2024-03-15 assembly: add images for assembly instruction
2024-03-15 README.de.md: erste Version der Aufbauanleitung
2024-03-15 README.de.md: 2 zusätzliche Bilder, besser erklärt
2024-03-17 apply bruder-jo's fix for spring - thx\!
    [spring-3mm.scad, spring-3mm.stl]
2024-03-17 add Pen Knob by Smuk3D (https://www.thingiverse.com/thing:1450115/files)
    [nut_knob_v1_5_1_M4.scad]
2024-03-17 refine inner wall
    [nut_knob_v1_5_1_M4.scad]
2024-03-21 improvements for better printability by bruder-jo - thx!!!
    [tpu-eierhalter.scad, tpu-pad-15x13.stl]
2024-03-23 improve eierhalter lagerseite for better printability - thx to bruder-jo!
    [tpu-eierhalter-lagerseite.stl]
2024-03-24 add hint for to get the steppers connected correctly at first try
2024-03-24 reorganize dir structure, add more print files
    [Box_Intersecting_Rods.stl, Faucet.stl, Pen_Stepper_Holder_Foot.stl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]
2024-03-24 add pics for assembly instructions
2024-03-24 add assembly instructions for mechanics
2024-03-26 inkscape plugin: disable steppers after plotting
2024-03-27 add spacer
    [spacer.scad, spacer.stl]
2024-03-27 update BOM
2025-04-18 Dev 2025 eh22 (#17)
    * decrease width of toolmount to fix #9
    * fix sequence for assembly: mechanics first, electronics next
    * add required tools
    * add Eierhalter Lagerseite to steps
    * refine print files
    * first part of cleanup
    * more fixes
    * add new pics
    * even more
    * fix file name
    * even more fixes
    * fix file name
    * fix format
    [Box_Intersecting_Rods.stl, Box_IntersectionNew.FCStd, Box_IntersectionNew.stl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]
2025-04-22 Arduino esp32 v2 to v3 (#27)
    * fix for arduino-esp32 v2->v3 migration,
    see https://github.com/espressif/arduino-esp32/blob/master/docs/en/migration_guides/2.x_to_3.0.rst#ledc
    and https://github.com/section77/eggbot77/issues/19
    * fix pin (2 -> 6)
    ---------
    Authored-by: Andreas Weber <andy@josoansi.de>
    [EBBHardware.cpp, config.h]
2026-04-03 Dev 2025 eh22 -> main (#28)
    * fix tool size
    * duplicate all changes to english version
    * add the big tpu pads
    * update filenames
    * update filenames
    * fix file names, fix text
    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
    [tpu-pad-18x15.stl]

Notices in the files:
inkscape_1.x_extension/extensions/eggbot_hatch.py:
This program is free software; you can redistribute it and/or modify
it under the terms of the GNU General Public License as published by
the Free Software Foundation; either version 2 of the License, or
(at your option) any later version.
